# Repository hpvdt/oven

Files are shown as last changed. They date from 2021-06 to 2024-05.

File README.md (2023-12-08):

# Oven Control System

Our team's generic composite oven controller. Used to maintain a desired two-step curing 
cycle recommended for the majority of our composites. Each step is defined with a target 
temperature, a ramp speed to reach it at (e.g. 2 degC/minute), and hold time at that 
temperature.

The control system is pretty simple, a single K-type thermocouple is used to monitor the 
temperature in the oven, and a simple "ON/OFF" scheme is used to operate the relay that 
controls the power to the heater. Turning ON when below a threshold, and then OFF once 
the upper threshold is surpassed.

User input is handled by a 16 button keypad, with a 20 by 4 character LCD screen used for 
feedback to the user to inform them of their input, and the current state of the oven.

## Code

With the exception of the display code (under "libraries") all the code was written by hand 
in the Arduino IDE. The main firmware is `oven_system` which is written for an Arduino Nano.

It was previously modified to include logging capabilities (`oven_system_with_logging`), 
and another version to operate using the serial interface for input/output in the absence 
of a keybad and/or a screen (`oven_system_no_display`). ***These variants have not been 
maintained to include recent improvements to the main code!***

In addition to the main code, we also prepared unit tests for each piece of hardware we were 
introducing to the system. In these we wrote the code needed to interact with each part as 
well as running some basic tests to exercise both the code and component. These are all in 
the "unit_tests" folder.

## Hardware

The current design is a small circuit board which has the ATmega328P microcontroller and 
the MAX6675 thermocouple chip. The microcontroller is set up to be programmed just like 
an Arduino Nano. Off board is the solid state relay used to regulate the heater, the 5V 
supply, keypad, and screen. This is all housed in a metal case repurposed from a failed 
power supply, with the terminal block used to connect the thermocouple, power, and heater.

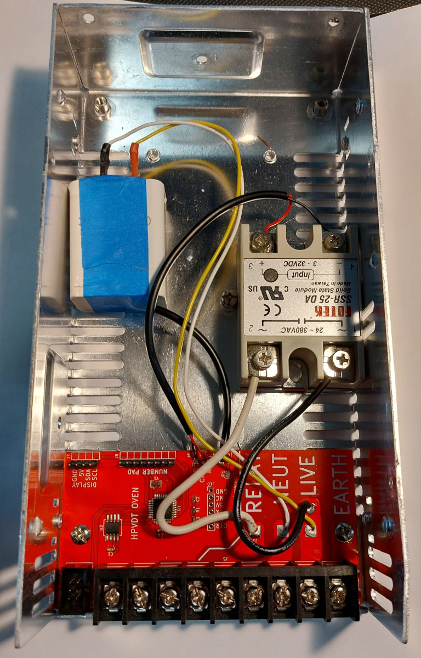
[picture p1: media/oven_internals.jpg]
The internal layout of the present oven system


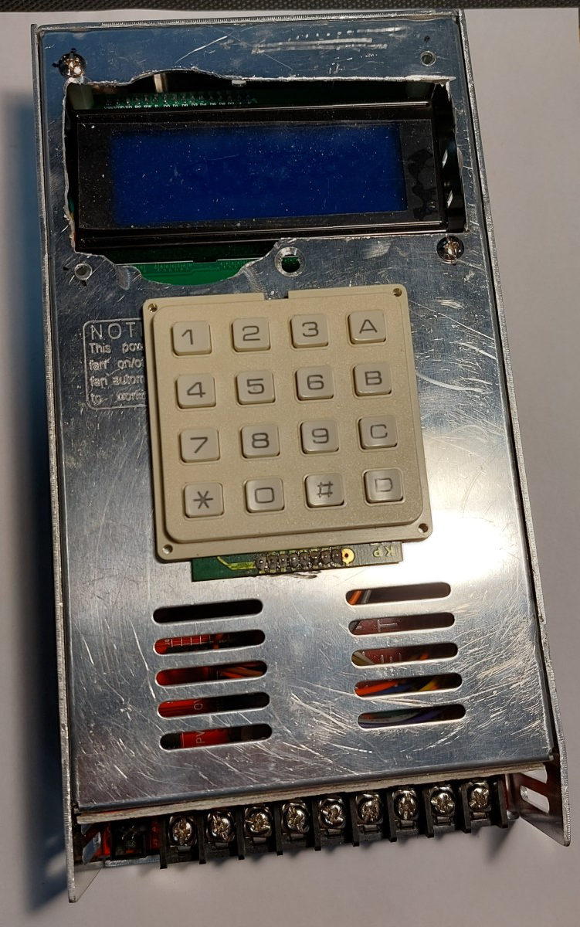
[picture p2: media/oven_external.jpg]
External view of the completed assembly


The current board was designed in KiCad 6, however my previous versions were designed in 
EAGLE. The most notable differences through iterations are:

- Embedding of the microcontroller and the MAX6675 directly to the main board
- Removal of the logging functionality since it was not used
- The earliest versions were designed to use thermistors instead of a thermocouple
- Previous designs weren't designed to fit in any particular enclosure

## TODO

A small to-do list of future features that could improve the system.

- [ ] Add some system to allow for recovery if power is interrupted
- [ ] Add some system to allow the system to be reset if needed
- [x] Figure out why SPI programming doesn't work if the MAX6675 is connected in any way
    - This was due to the MAX6675 not having a pullup on nCS, so it was active during programming of the ATmega and interfered on the SPI bus.
    - This **should** be revised in future hardware revisions

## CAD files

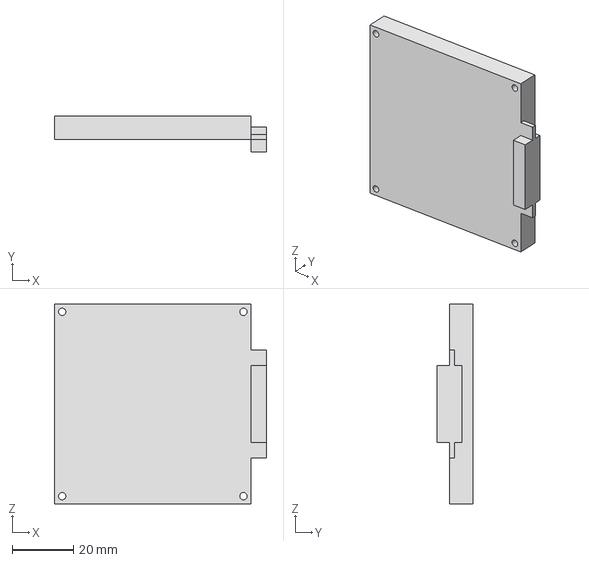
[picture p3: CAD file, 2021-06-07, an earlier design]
hardware/Old Hardware/CAD Files of Parts/Keypad.stp
69.0 x 11.6 x 65.0 mm

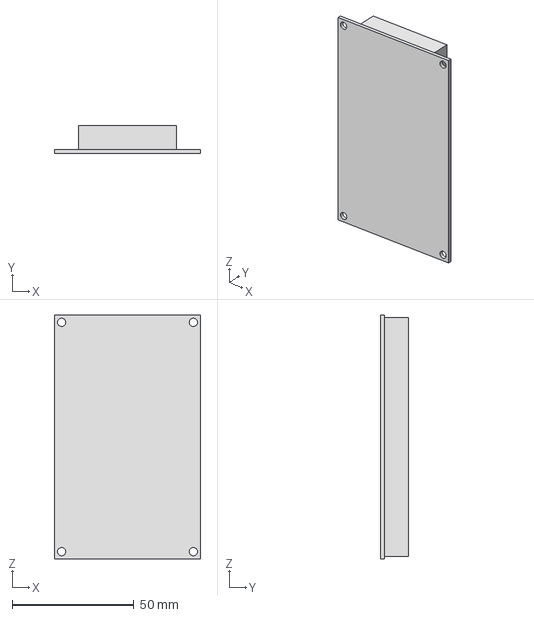
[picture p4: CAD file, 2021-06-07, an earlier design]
hardware/Old Hardware/CAD Files of Parts/LCD Screen.stp
60.0 x 11.6 x 100.0 mm

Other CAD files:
hardware/Old Hardware/CAD Files of Parts/Case.ipt
hardware/Old Hardware/CAD Files of Parts/Keypad.ipt
hardware/Old Hardware/CAD Files of Parts/LCD Screen.ipt
hardware/Old Hardware/CAD Files of Parts/OldVersions/Case.0002.ipt
hardware/Old Hardware/CAD Files of Parts/OldVersions/Keypad.0001.ipt
hardware/Old Hardware/CAD Files of Parts/OldVersions/LCD Screen.0001.ipt
hardware/Old Hardware/CAD Files of Parts/OldVersions/PCB.0001.ipt
hardware/Old Hardware/CAD Files of Parts/Oven Control.iam
hardware/Old Hardware/CAD Files of Parts/PCB.ipt

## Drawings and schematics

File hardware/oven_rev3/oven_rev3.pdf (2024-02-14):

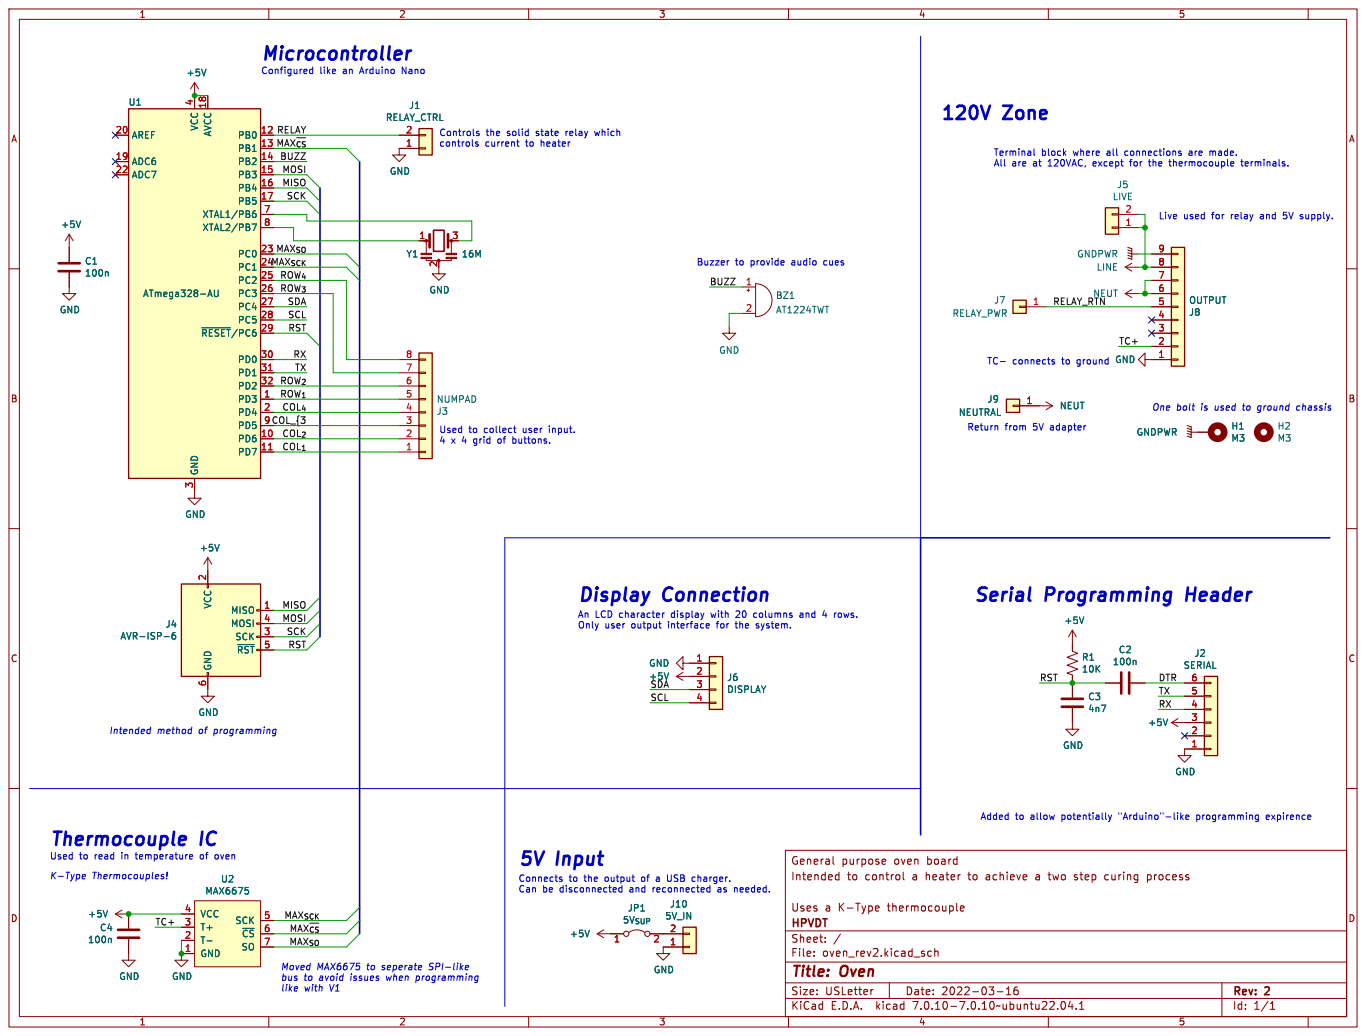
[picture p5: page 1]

BUZZ SCK
SCL MISO MOSI RST

Live used for relay and 5V supply.

2 SCK 3 MOSI 4 ~{RST}5 GND

Intended method of programming

Moved MAX6675 to seperate SPI-like
bus to avoid issues when programming
like with V1

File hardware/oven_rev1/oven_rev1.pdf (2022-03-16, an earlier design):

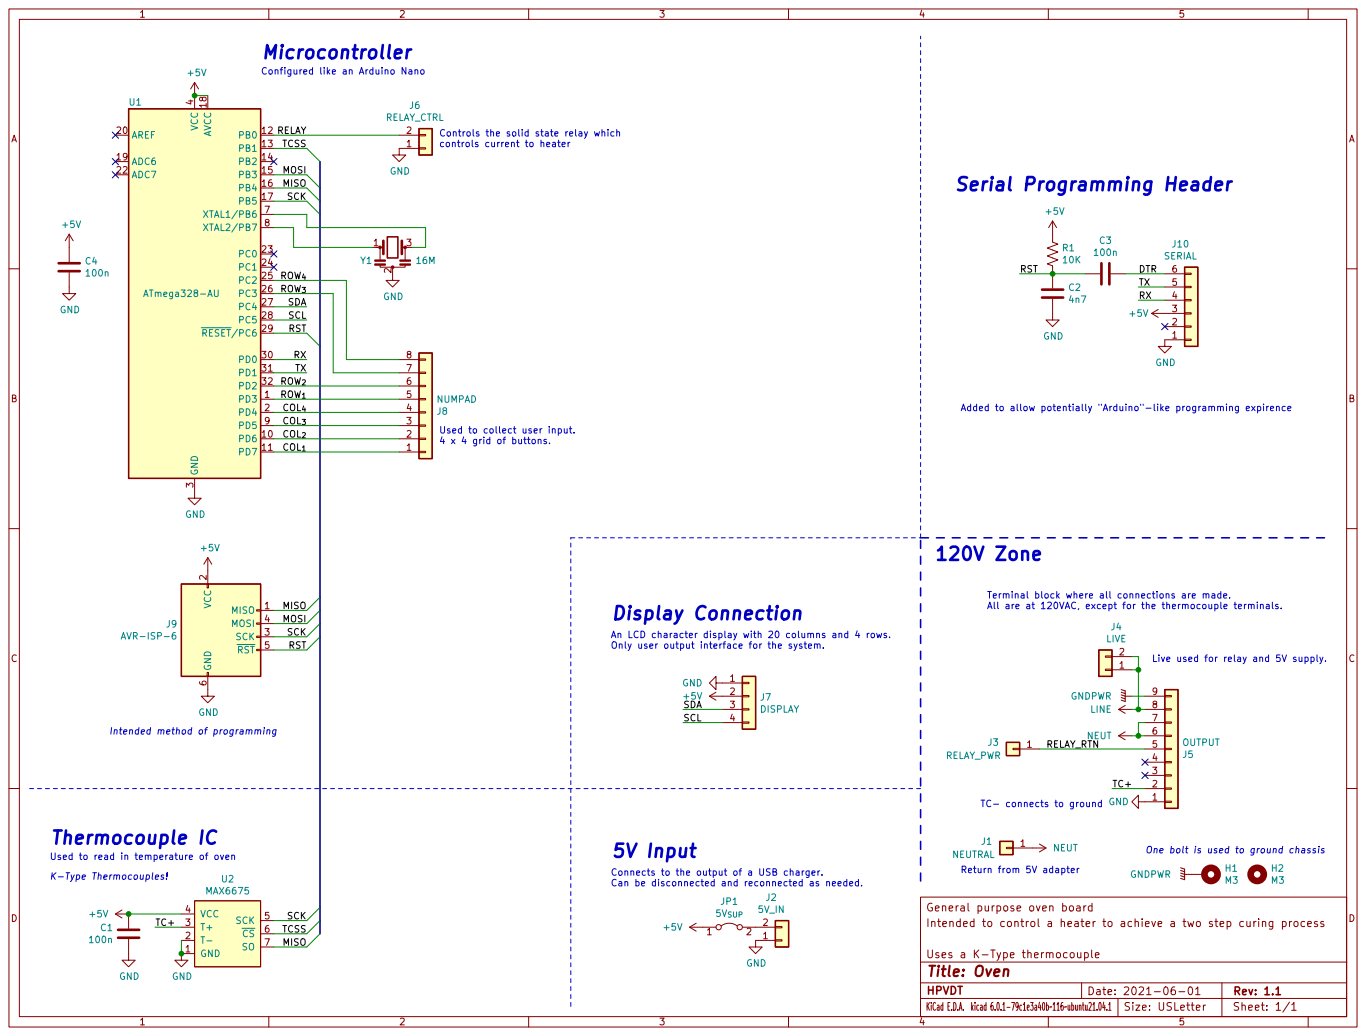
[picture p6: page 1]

Controls the solid state relay which controls current to heater Used to collect user input.

Configured like an Arduino Nano

3 PD0 30 PD1 31 PD2 32 VCC
ROW_{4} SDARX COL_{4} RST MISO MISO
SCK

Added to allow potentially "Arduino"-like programming expirence

COL_{3 | 3

COL_{1} | 1

2 SCK 3 MOSI 4 ~{RST} 5 GND

Live used for relay and 5V supply. Terminal block where all connections are made. All are at 120VAC, except for the thermocouple terminals.

An LCD character display with 20 columns and 4 rows.
Only user output interface for the system.

Intended method of programming

Connects to the output of a USB charger. Can be disconnected and reconnected as needed.

General purpose oven board KiCad E.D.A. kicad 6.0.1-79c1e3a40b~116~ubuntu21.04.1
Intended to control a heater to achieve a two step curing process

HPVDT Uses a K-Type thermocouple

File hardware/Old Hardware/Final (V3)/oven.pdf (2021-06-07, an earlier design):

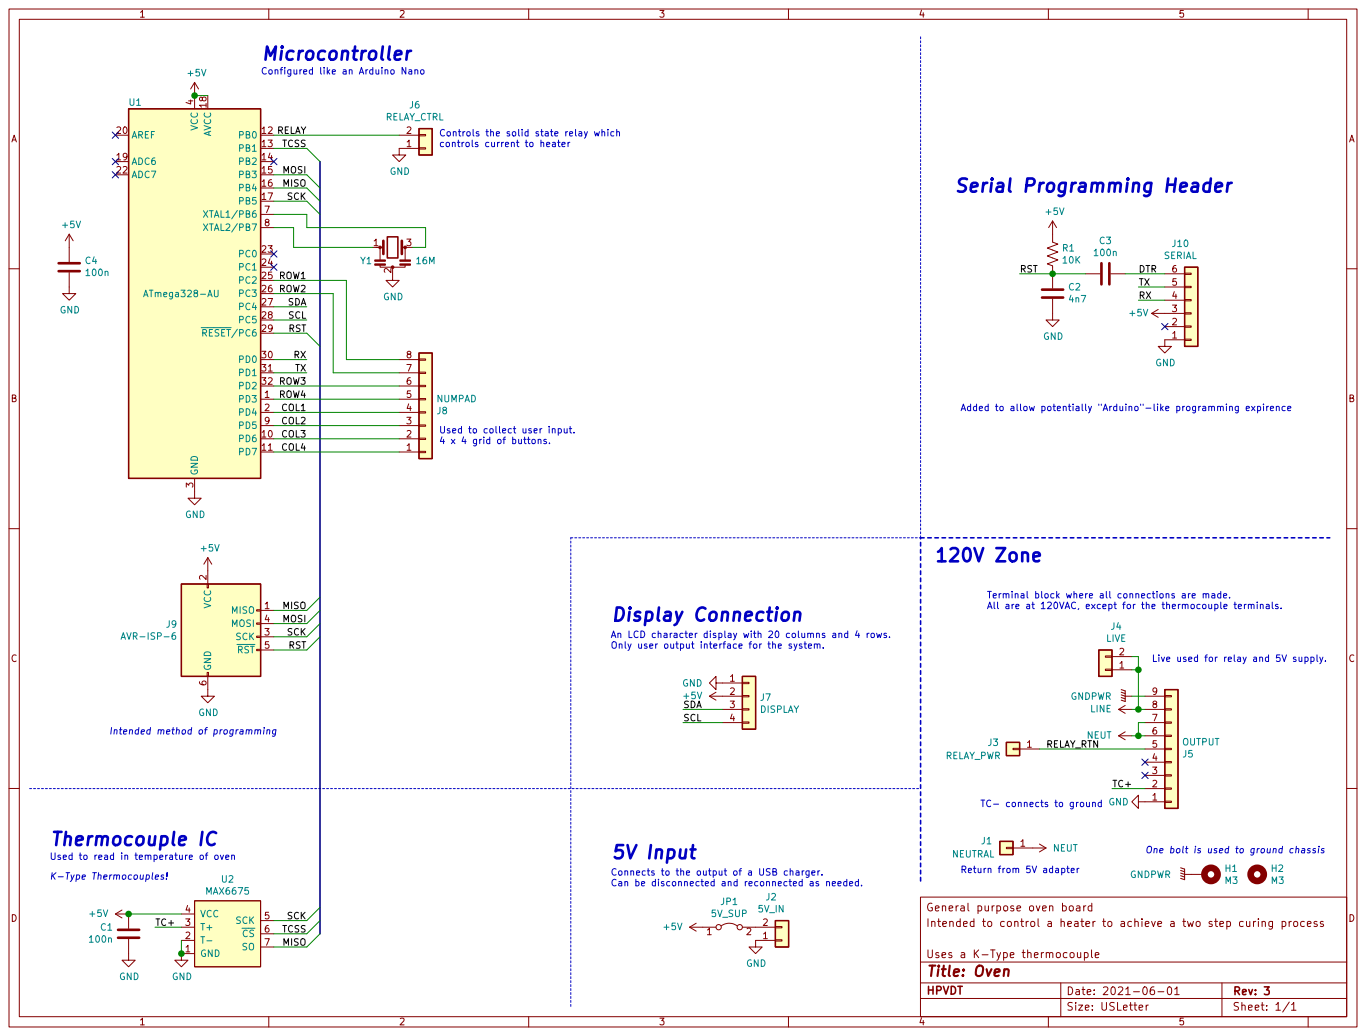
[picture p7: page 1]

Configured like an Arduino Nano

Added to allow potentially "Arduino"-like programming expirence

Used to collect user input.
4 x 4 grid of buttons.

2 SCK 3 MOSI 4 RST 5 GND

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

Intended method of programming

TC- connects to ground

One bolt is used to ground chassis

Connects to the output of a USB charger. Can be disconnected and reconnected as needed.

Intended to control a heater to achieve a two step curing process

HPVDT Uses a K-Type thermocouple

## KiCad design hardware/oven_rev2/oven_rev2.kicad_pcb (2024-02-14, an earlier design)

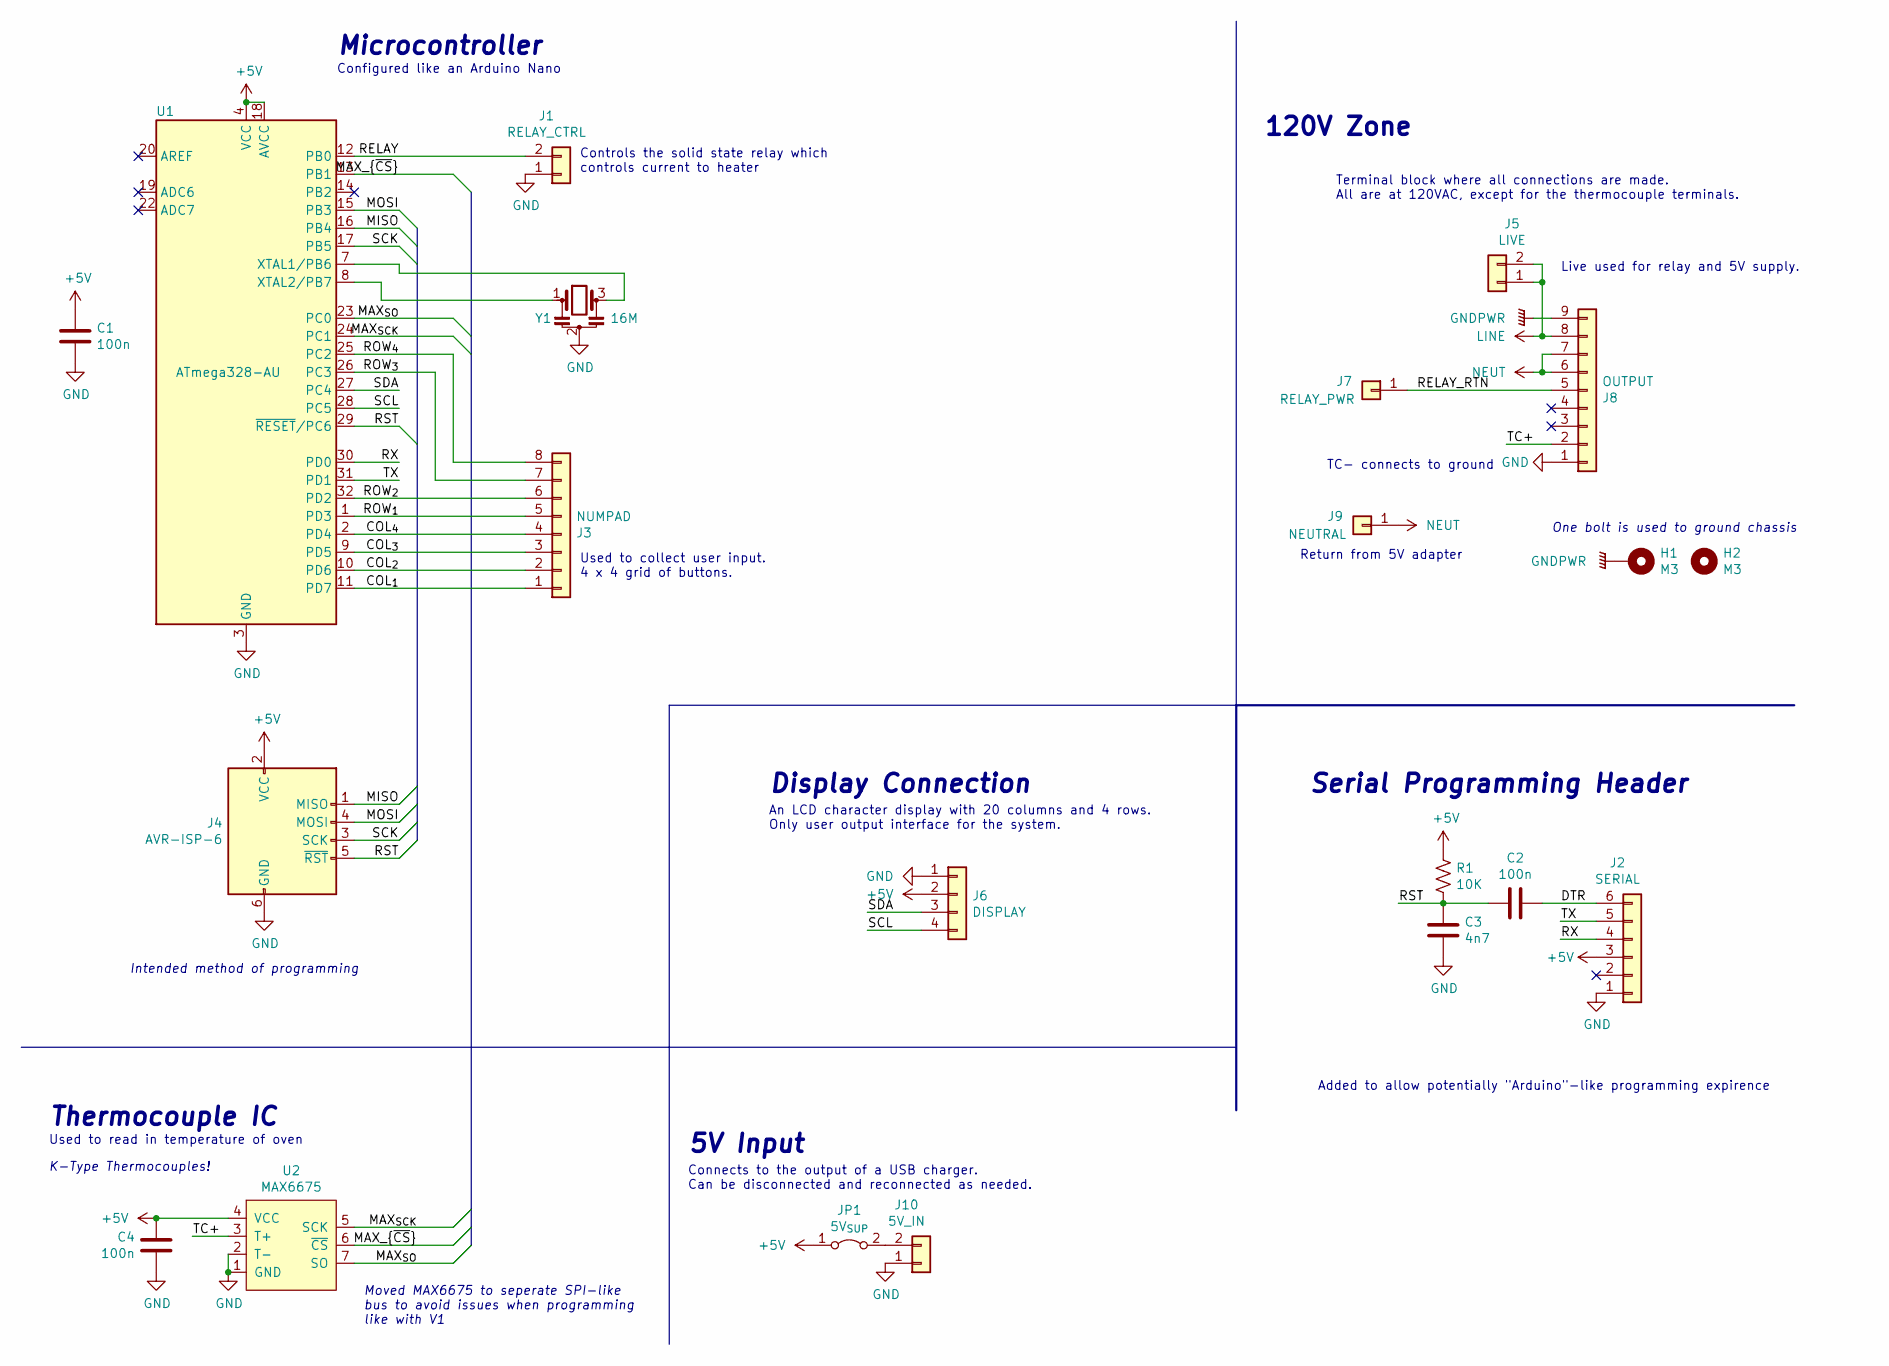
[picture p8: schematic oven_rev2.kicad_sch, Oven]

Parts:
C1, C2, C4: 100n; C_0603_1608Metric
C3: 4n7; C_0603_1608Metric
H1: M3; MountingHole_3.5mm_Pad_Via
H2: M3; MountingHole_3.5mm
J1: RELAY_CTRL; PinHeader_1x02_P2.54mm_Horizontal
J2: SERIAL; PinHeader_1x06_P2.54mm_Vertical
J3: NUMPAD; PinHeader_1x08_P2.54mm_Horizontal
J4: AVR-ISP-6; IDC-Header_2x03_P2.54mm_Vertical
J5: LIVE; SolderWire-2sqmm_1x02_P7.8mm_D2mm_OD3.9mm
J6: DISPLAY; PinHeader_1x04_P2.54mm_Horizontal
J7: RELAY_PWR; SolderWire-2sqmm_1x01_D2mm_OD3.9mm
J8: OUTPUT; 9POS-TERMBLOCK
J9: NEUTRAL; SolderWire-2sqmm_1x01_D2mm_OD3.9mm
J10: 5V_IN; PinHeader_1x02_P2.54mm_Horizontal
JP1: 5V_{SUP}; SolderJumper-2_P1.3mm_Bridged_Pad1.0x1.5mm
R1: 10K; R_0603_1608Metric
U1: ATmega328-AU; TQFP-32_7x7mm_P0.8mm
U2: MAX6675; SO-8_5.3x6.2mm_P1.27mm
Y1: 16M; Resonator_SMD_muRata_CSTxExxV-3Pin_3.0x1.1mm

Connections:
+5V: C1.2, C4.2, J2.3, J4.2 (VCC), J6.2, JP1.1 (A), R1.1, U1.4 (VCC), U1.6 (VCC), U1.18 (AVCC), U2.4 (VCC)
/COL_{1}: J3.1, U1.11 (PD7)
/COL_{2}: J3.2, U1.10 (PD6)
/COL_{3}: J3.3, U1.9 (PD5)
/COL_{4}: J3.4, U1.2 (PD4)
/DTR: C2.1, J2.6
/MAX_{SCK}: U1.24 (PC1), U2.5 (SCK)
/MAX_{SO}: U1.23 (PC0), U2.7 (SO)
/MAX_{~CS}: U1.13 (PB1), U2.6 (~CS)
/MISO: J4.1 (MISO), U1.16 (PB4)
/MOSI: J4.4 (MOSI), U1.15 (PB3)
/RELAY: J1.2, U1.12 (PB0)
/RELAY_RTN: J7.1, J8.5
/ROW_{1}: J3.5, U1.1 (PD3)
/ROW_{2}: J3.6, U1.32 (PD2)
/ROW_{3}: J3.7, U1.26 (PC3)
/ROW_{4}: J3.8, U1.25 (PC2)
/RST: C2.2, C3.2, J4.5 (~RST), R1.2, U1.29 (~RESET/PC6)
/RX: J2.4, U1.30 (PD0)
/SCK: J4.3 (SCK), U1.17 (PB5)
/SCL: J6.4, U1.28 (PC5)
/SDA: J6.3, U1.27 (PC4)
/TC+: J8.2, U2.3 (T+)
/TX: J2.5, U1.31 (PD1)
GND: C1.1, C3.1, C4.1, J1.1, J2.1, J4.6 (GND), J6.1, J8.1, J10.1, U1.3 (GND), U1.5 (GND), U1.21 (GND), U2.1 (GND), U2.2 (T-), Y1.2
GNDPWR: H1.1, J8.9
LINE: J5.1, J5.2, J8.8
NEUT: J8.6, J8.7, J9.1
unnamed: J10.2, JP1.2 (B)
unnamed: U1.7 (XTAL1/PB6), Y1.3
unnamed: U1.8 (XTAL2/PB7), Y1.1

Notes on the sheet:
Moved MAX6675 to seperate SPI-like bus to avoid issues when programming like with V1
One bolt is used to ground chassis
Live used for relay and 5V supply.
Used to read in temperature of oven
120V Zone
Controls the solid state relay which controls current to heater
Microcontroller
5V Input
Display Connection
Return from 5V adapter
Connects to the output of a USB charger. Can be disconnected and reconnected as needed.
Intended method of programming
An LCD character display with 20 columns and 4 rows. Only user output interface for the system.
Added to allow potentially "Arduino"-like programming expirence
TC- connects to ground
Configured like an Arduino Nano
Serial Programming Header
Thermocouple IC
K-Type Thermocouples!
Terminal block where all connections are made. All are at 120VAC, except for the thermocouple terminals.
Used to collect user input. 4 x 4 grid of buttons.

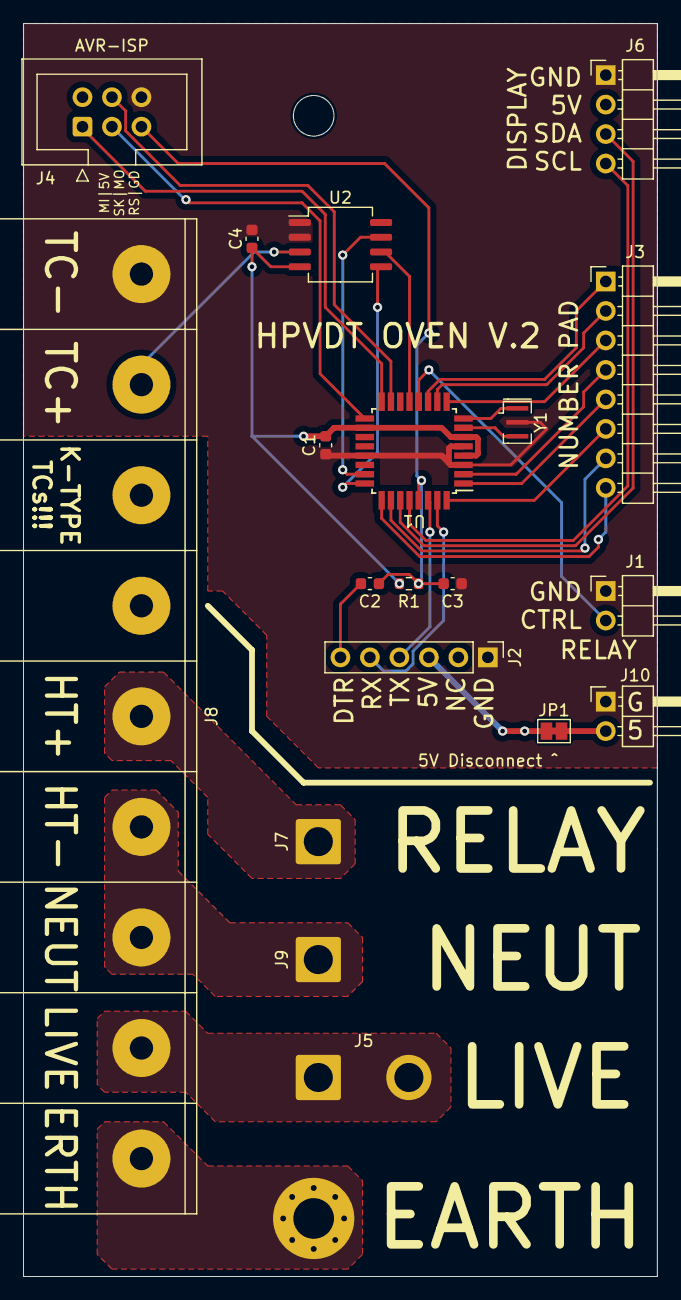
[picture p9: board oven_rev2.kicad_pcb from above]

Board: 2 copper layers, 54.6 x 108.0 mm, 21 parts (0 on the bottom side), 31 nets.

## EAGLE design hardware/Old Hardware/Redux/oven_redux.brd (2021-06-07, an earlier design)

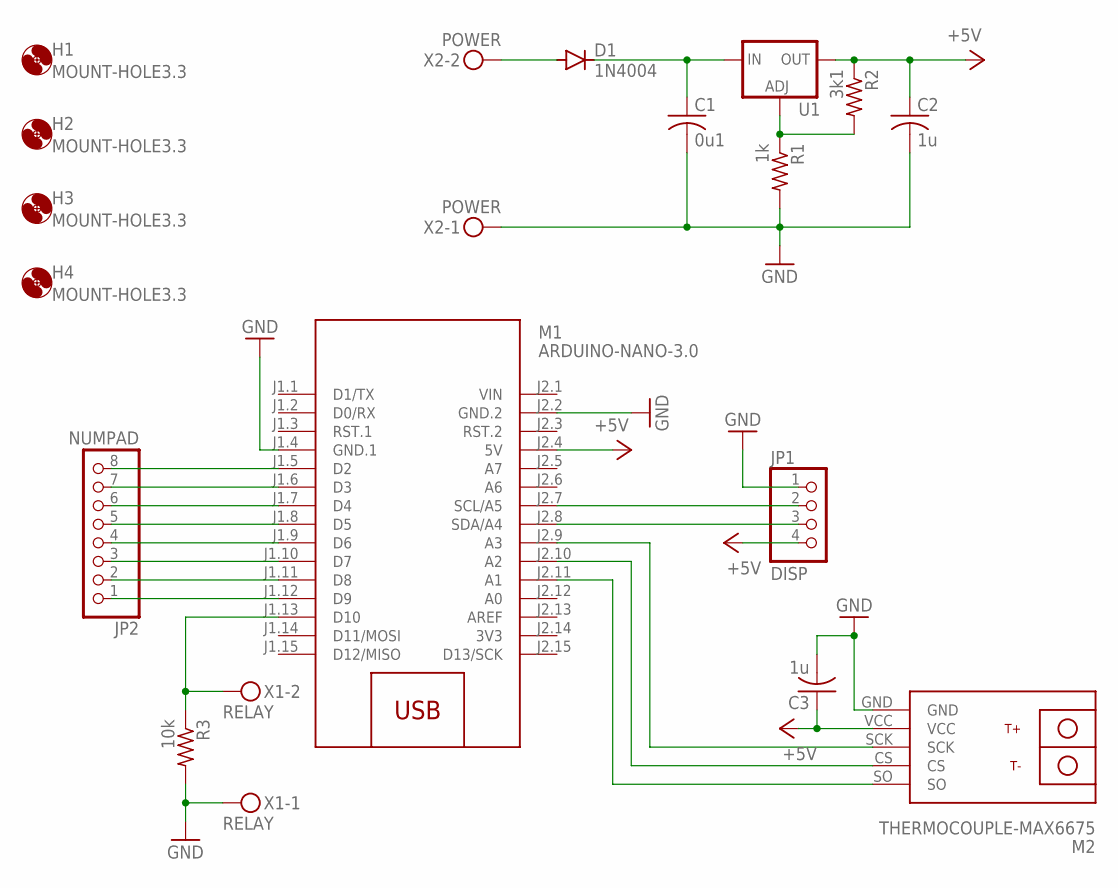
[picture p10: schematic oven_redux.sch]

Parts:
C1: 0u1; C025-050X050
C2, C3: 1u; C025-050X050
D1: 1N4004; DO41-10
H1, H2, H3, H4: MOUNT-HOLE3.3; 3,3
JP1: DISP; 1X04
JP2: NUMPAD; 1X08
M1: ARDUINO-NANO-3.0
M2: THERMOCOUPLE-MAX6675
R1: 1k; 0204/7
R2: 3k1; 0204/7
R3: 10k; 0204/7
U1: LM317TL; 317TL
X1: RELAY; MKDSN1,5/2-5,08
X2: POWER; MKDSN1,5/2-5,08

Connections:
3V3: M1.J2.14 (3V3)
+5V: C2.1, C3.1, JP1.4, M1.J2.4 (5V), M2.VCC, R2.1, U1.2 (OUT)
GND: C1.2, C2.2, C3.2, JP1.1, M1.J1.4 (GND.1), M1.J2.2 (GND.2), M2.GND, R1.2, R3.2, X1.1, X2.1
unnamed: JP2.1, M1.J1.12 (D9)
unnamed: JP2.2, M1.J1.11 (D8)
unnamed: JP2.3, M1.J1.10 (D7)
unnamed: JP2.4, M1.J1.9 (D6)
unnamed: JP2.5, M1.J1.8 (D5)
unnamed: JP2.6, M1.J1.7 (D4)
unnamed: JP2.7, M1.J1.6 (D3)
unnamed: JP2.8, M1.J1.5 (D2)
unnamed: JP1.2, M1.J2.7 (SCL/A5)
unnamed: R1.1, R2.2, U1.1 (ADJ)
unnamed: C1.1, D1.C, U1.3 (IN)
unnamed: D1.A, X2.2
unnamed: JP1.3, M1.J2.8 (SDA/A4)
unnamed: M1.J2.9 (A3), M2.SCK
unnamed: M1.J2.10 (A2), M2.CS
unnamed: M1.J1.13 (D10), R3.1, X1.2
unnamed: M1.J2.11 (A1), M2.SO
VIN: M1.J2.1 (VIN)

Board: 2 copper layers, 18 parts (0 on the bottom side), 19 nets, no tracks yet.

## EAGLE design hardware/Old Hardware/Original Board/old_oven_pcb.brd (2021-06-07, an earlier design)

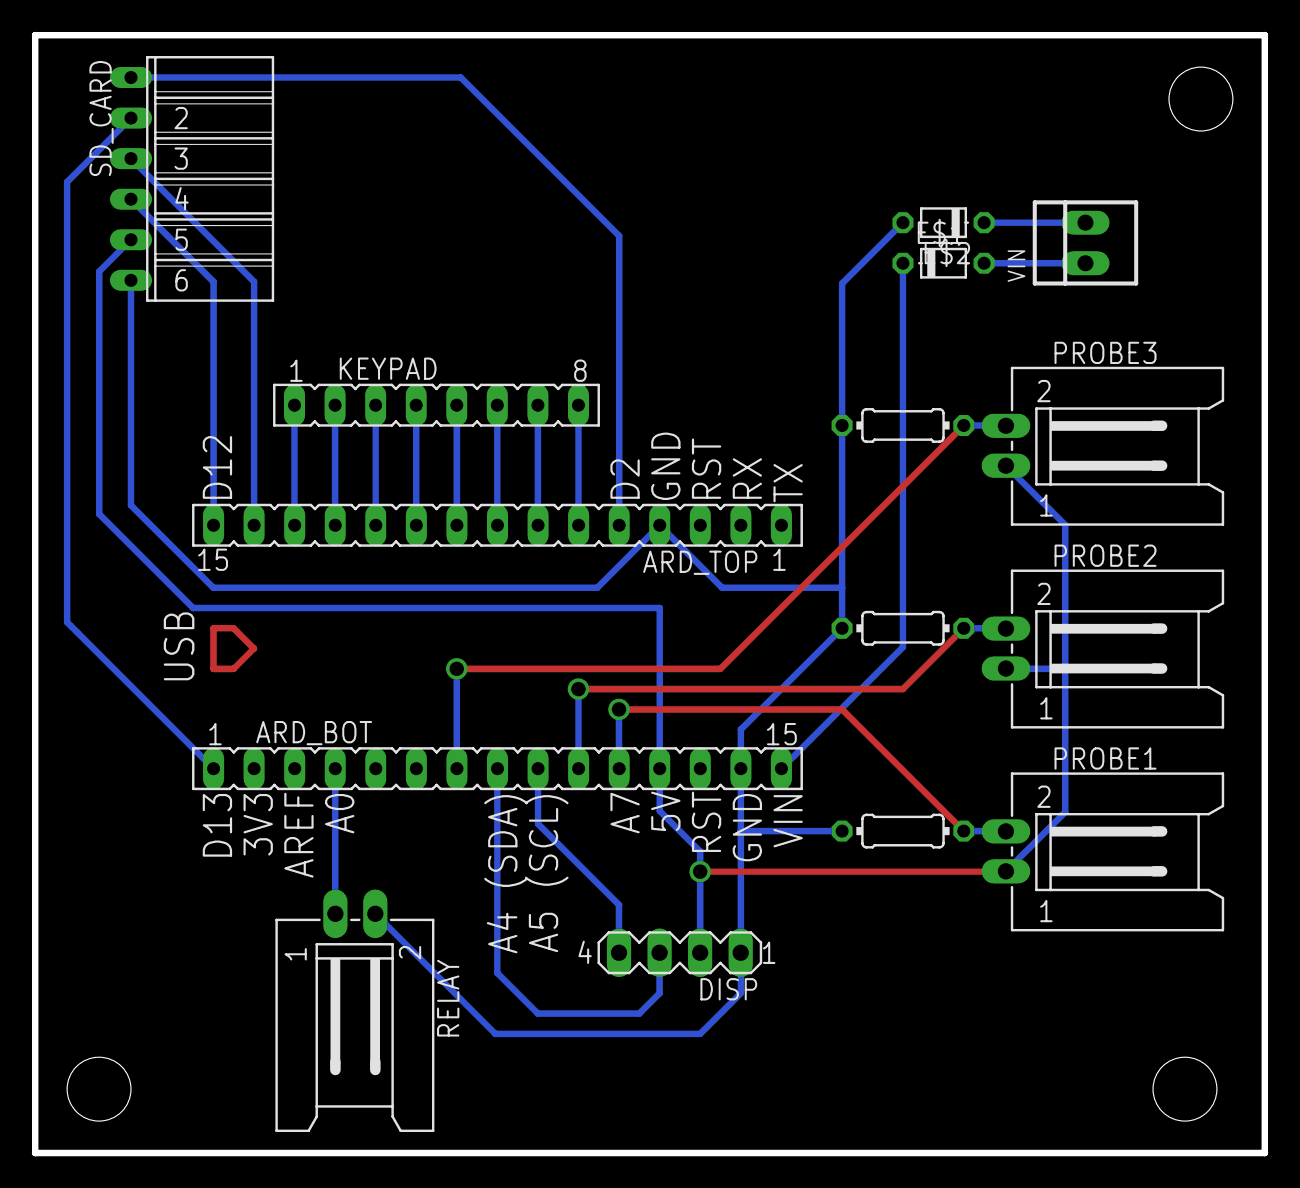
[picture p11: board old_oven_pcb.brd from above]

Board: 2 copper layers, 77.0 x 70.0 mm, 15 parts (0 on the bottom side), 23 nets.

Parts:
ARD_BOT: FE15
ARD_TOP: FE15
DISP: MA04-1
E$1, E$2: D-5
E$3, E$4, E$6: 10k; 0204/7
KEYPAD: FE08
PROBE1, PROBE2, PROBE3: L02P
RELAY: L02P
SD_CARD: FE06W
VIN: 22-23-2021

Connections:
5V: ARD_BOT.12, DISP.2, PROBE1.1, PROBE2.1, PROBE3.1, SD_CARD.5
D3: ARD_TOP.6, KEYPAD.8
D4: ARD_TOP.7, KEYPAD.7
D5: ARD_TOP.8, KEYPAD.6
D6: ARD_TOP.9, KEYPAD.5
D7: ARD_TOP.10, KEYPAD.4
D8: ARD_TOP.11, KEYPAD.3
D9: ARD_TOP.12, KEYPAD.2
D10: ARD_TOP.5, SD_CARD.1
D13: ARD_BOT.1, SD_CARD.2
GND: ARD_BOT.14, ARD_TOP.4, DISP.1, E$2.A, E$3.2, E$4.2, E$6.2, RELAY.2, SD_CARD.6
PROBE1: ARD_BOT.11, E$4.1, PROBE1.2
PROBE2: ARD_BOT.10, E$3.1, PROBE2.2
PROBE3: ARD_BOT.7, E$6.1, PROBE3.2
RELAY: ARD_BOT.4, RELAY.1
S$1: ARD_TOP.13, KEYPAD.1
S$3: ARD_TOP.15, SD_CARD.4
S$4: ARD_TOP.14, SD_CARD.3
SCL: ARD_BOT.9, DISP.4
SDA: ARD_BOT.8, DISP.3
V+: E$1.A, VIN.1
V-: E$2.C, VIN.2
VIN: ARD_BOT.15, E$1.C

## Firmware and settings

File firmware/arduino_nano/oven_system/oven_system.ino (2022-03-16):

#include <Wire.h>
#include <LiquidCrystal_I2C.h>

// A4 is SDA
// A5 is SCL

LiquidCrystal_I2C lcd(0x27, 2, 1, 0, 4, 5, 6, 7, 3, POSITIVE);
//LiquidCrystal_I2C lcd(0x27, 4, 5, 6, 0, 1, 2, 3, 7, POSITIVE);

// Keypad config
const byte row1 = 3; // Row 1 pin
const byte row2 = 2;
const byte row3 = A3;
const byte row4 = A2;
const byte col1 = 7; // Column 1 pin
const byte col2 = 6;
const byte col3 = 5;
const byte col4 = 4;

char buttonPressed;
// Keypad works by detecting the intersection of a row and col pulling down an input. (A column pulling the row down)

// MAX6675 Pins
const byte MAX_SCK = A1;
const byte MAX_CS = 9;
const byte MAX_SO = A0;

// Heater 
const byte heater = 12;  // Heater relay pin
bool heaterState;       // State variable

// Control variables
int screen, field;                  // Used for display
const int numScreens = 4;           // Used as a limit for number of distinct screens
const int numFields = 3;            // Used as a limit for number of fields on a screen

// User input field configuration
const int maxFieldLength = 6;        // Max length of entered data
String fields[9];                    // Used to display entry data (should have numFields * numScreens elements)

int stage = 1;                          // Records cooking stage
double targetTemp, curTemp;              // Target and current temp
double temperature[5];                   // Used to store temp set points
const double tempTol = 5;                // Used as tolerance for over temp - IMPORTANT
unsigned long setPointTimes[5];         // Used for changes
double elapsedTime;                      // Used for status display
String endTime;                         // Used for status display (to minimize repeated instructions)

void setup() {
  lcd.begin(20, 4);   // Set up display. 20 character in 4 rows
  lcd.clear();        //Clear the display

  // Keypad setup
  pinMode(row1, INPUT_PULLUP); pinMode(row2, INPUT_PULLUP); pinMode(row3, INPUT_PULLUP); pinMode(row4, INPUT_PULLUP);
  pinMode(col1, OUTPUT); pinMode(col2, OUTPUT); pinMode(col3, OUTPUT); pinMode(col4, OUTPUT);

  pinMode(heater, OUTPUT);            // Controls relay
  heaterState = LOW;                  // Off by default
  digitalWrite(heater, heaterState);

  // Splash screen
  printCenter(1, F("Oven Control System"));
  printCenter(2, F("Designed for HPDVT"));
  delay(1000);
  lcd.clear();

  // Initialization
  screen = 0;
  field = 0;
}

void loop() {
  // Screen
  switch (screen) {
    case 0: // Setup first point
      printLeft(0, F("Target Temp"));
      printLeft(1, F("Rise Rt. c/m"));
      printLeft(2, F("Hold Time (m)"));
      printCenter(3, F("Stg 1"));
      printCursor();
      for (int i = 0; i < numFields; i++) {
        printRight(i, fields[i + numFields * screen]);
      }
      printRight(3, "Stg 2>");

      buttonAction(); // Performs button action
      break;
    case 1: // Second point config
      printLeft(0, F("Target Temp"));
      printLeft(1, F("Rise Rt. c/m"));
      printLeft(2, F("Hold Time (m)"));
      printLeft(3, F("<Stg 1"));
      printCenter(3, F("Stg 2"));
      printCursor();
      for (int i = 0; i < numFields; i++) {
        printRight(i, fields[i + numFields * screen]);
      }
      printRight(3, "Strt>");

      buttonAction(); // Performs button action

      // Check if starting oven
      if (screen == (numScreens - 2)) {
        stage = 1; // Entered first stage
        
        //Sets temperature points
        temperature[0] = readTemperature(MAX_SCK, MAX_CS, MAX_SO); // Record starting temp
        temperature[1] = fields[0].toFloat();
        temperature[2] = temperature[1];
        temperature[3] = fields[numFields].toFloat();
        temperature[4] = temperature[3];

        // Gets times
        // Times are (target - start) / ramp rate
        elapsedTime = 0;
        setPointTimes[0] = actualMillis();                                                          // Start time
        setPointTimes[1] = (temperature[1] - temperature[0]) * 60000 / fields[1].toFloat();   // Uses rate and difference to find ramp time
        setPointTimes[2] = fields[2].toFloat() * 60000;                                       // Records hold time
        setPointTimes[3] = (temperature[3] - temperature[2]) * 60000 / fields[1].toFloat();   // Second ramp
        setPointTimes[4] = fields[2 + numFields].toFloat() * 60000;                           // Last hold

        for (int i = 1; i <= 4; i++) {
          setPointTimes[i] += setPointTimes[i - 1]; //Makes the times cummulative
        }
        endTime = int(ceil((setPointTimes[4] - setPointTimes[0]) / 60000)); // Records the end as a string for status display
      }
      break;
      
    case 2: // Runtime
      // Control
      // Gets linearly interpolated temperature based on time and bounding set points
      // map() outputs long int, needed floats so I adjusted their source code
      targetTemp = (actualMillis() - setPointTimes[stage - 1]) * (temperature[stage] - temperature[stage - 1]);
      targetTemp /= (setPointTimes[stage] - setPointTimes[stage - 1]);
      targetTemp += temperature[stage - 1];
      curTemp = readTemperature(MAX_SCK, MAX_CS, MAX_SO); // Gets current temp

      if (curTemp < targetTemp) {
        heaterState = HIGH;                   // Too cold
        digitalWrite(heater, heaterState);
      }
      else if (curTemp > (targetTemp + 1)) {
        heaterState = LOW;                    // Too hot
        digitalWrite(heater, heaterState);
      }
      
      // Time
      if (actualMillis() > setPointTimes[stage]) stage++; // Checks if approriate stage
      elapsedTime = actualMillis() - setPointTimes[0];    // Elaplsed time in ms
      elapsedTime /= 60000;                         // Elapsed time in minutes
      
      // Screen stuff
      printLeft(0, F("Cur/Tar"));
      printLeft(1, F("Elp/End"));
      printLeft(2, F("Heater"));
      printCenter(3, F("Oven Status"));

      // Fields
      fields[numFields * screen] = "  ";
      fields[numFields * screen] += oneDecimal(curTemp);       // Temp
      fields[numFields * screen] += "/";
      fields[numFields * screen] += oneDecimal(targetTemp);   // Target

      fields[1 + numFields * screen] = oneDecimal(elapsedTime);   // Time
      fields[1 + numFields * screen] += "/";
      fields[1 + numFields * screen] += endTime;                  // End

      if (heaterState) {
        fields[2 + numFields * screen] = " ON";  // Heater ON
      }
      else {
        fields[2 + numFields * screen] = "OFF"; // Heater OFF
      }

      for (int i = 0; i < numFields; i++) {
        printRight(i, fields[i + numFields * screen]);
      }

      // Check for finish (past stage 4)
      if (stage == 5) {
        screen++; // Go to next step
        lcd.clear();
        
        // Turn off heater
        heaterState = LOW;                  
        digitalWrite(heater, heaterState);
      }
      delay(300); // Extending cycle time during run time
      break;
      
    case 3: // Finished
      printCenter(0, F("Process Complete"));
      printCenter(1, F("Oven is disabled"));
      printLeft(3, "Cur. Temp");
      printRight(3, "   " + oneDecimal(readTemperature(MAX_SCK, MAX_CS, MAX_SO)));

      // Turn off heater
      heaterState = LOW;                  
      digitalWrite(heater, heaterState);
      
      delay(1000);
      break;
  }

  delay(25);
}

void buttonAction() {
  buttonPressed = checkKeypad(); // Get key pressed, if any
  
  switch (buttonPressed) {
    case 'x':
      break; // Nothing was pressed
      
    // Changing fields
    case 'A':
      field--;
      lcd.clear();
      field = constrain(field, 0, numFields - 1);
      break;
    case 'B':
      field++;
      lcd.clear();
      field = constrain(field, 0, numFields - 1);
      break;

    // Next screen
    case 'C':
      screen++;
      lcd.clear();
      screen = constrain(screen, 0, numScreens - 1);
      field = 0;
      break;
    case 'D':
      screen--;
      lcd.clear();
      screen = constrain(screen, 0, numScreens - 1);
      field = 0;
      break;

    // Backspace
    case '#':
      if (fields[field + numFields * screen].length() > 0) {
        lcd.clear();
        fields[field + numFields * screen].remove(fields[field + numFields * screen].length() - 1); // Removes last character
      }
      break;

    // Adding digits and decimal places is done by concatenating the string
    default:
      if (buttonPressed == '*') {
        buttonPressed = '.'; // Decimal
      }
      // Only adds if not at full length
      if ( fields[field + numFields * screen].length() < maxFieldLength){
        fields[field + numFields * screen] += buttonPressed;
      }
      break;
  }
}

// Function used to return a better approximation of time elasped
unsigned long actualMillis() {
  unsigned long trueMillis = millis();

  // millis() returns roughly 971 "milliseconds" per actual second due to the way millis() is set up with timers.
  // Scaling it up by a factor of 1.024 is needed to get roughly 1000 counts per actual second.
  // To keep it to integer math dividing by 125, multiplying by 128 is used.
  
  trueMillis = trueMillis / 125;
  trueMillis = trueMillis * 128;
  
  // Multiplication after division to avoid overflows with long work times
  
  return trueMillis;
}

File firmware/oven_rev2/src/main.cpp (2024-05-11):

#include <Arduino.h>
#include <Wire.h>
#include <LiquidCrystal_I2C.h>

#include "display.hpp"
#include "keypad.hpp"
#include "main.hpp"
#include "temperature.hpp"
#include "watchdog.hpp"

// Heater 
const byte heater = PIN_PB0;          // Heater relay pin
bool heaterState;                     // Heater state

// Control variables
int screen, field;                    // Used for display state
const int numScreens = 4;             // Used as a limit for number of distinct screens
const int numFields = 3;              // Used as a limit for number of fields on a screen

// User input field configuration
const int maxFieldLength = 6;         // Max length of entered data
String fields[numFields][numScreens]; // Data fields on each screen

int bakeStage = 1;                    // Records baking stage
float temperature[5];                 // Stores temperature set points
const float tempTol = 3.0;            // Tolerance for under temperature - IMPORTANT!
unsigned long setPointTimes[5];       // Records time for changes
String endTime;                       // Used for status display (to minimize repeated calculation)

void setup() {
  disableWatchdog(); // Needs to go first to prevent repeated watchdog resets

  setupKeypad();
  setupTemperature();

  // Set heater to start off until programmed
  pinMode(heater, OUTPUT);
  heaterState = LOW;
  digitalWrite(heater, heaterState);

  setupDisplay();

  screen = 0;
  field = 0;

  enableWatchdog(); 
  // NOTE: Currently the screen will shutdown until a complete power cycle after WDT reset
}

void loop() {
  // Screen
  switch (screen) {
    case 0: // Setup first point
      printLeft(0, F("Target Temp"));
      printLeft(3, oneDecimal(readTemperature()) + "C "); // Show temp on initial screen for error check
      printLeft(1, F("Rise Rt. c/m"));
      printLeft(2, F("Hold Time (m)"));
      printCenter(3, F("Stg 1"));
      printCursor();
      for (int i = 0; i < numFields; i++) printRight(i, fields[i][screen]);
      printRight(3, "Stg 2>");

      heaterState = LOW;

      buttonAction(); // Performs button action
      break;
    case 1: // Second point config
      printLeft(0, F("Target Temp"));
      printLeft(1, F("Rise Rt. c/m"));
      printLeft(2, F("Hold Time (m)"));
      printLeft(3, F("<Stg 1"));
      printCenter(3, F("Stg 2"));
      printCursor();
      for (int i = 0; i < numFields; i++) printRight(i, fields[i][screen]);
      printRight(3, "Strt>");

      heaterState = LOW;

      buttonAction(); // Performs button action

      // Check if starting oven
      if (screen == (numScreens - 2)) {
        bakeStage = 1; // Entered first stage
        
        //Sets temperature points
        temperature[0] = readTemperature(); // Record starting temp
        temperature[1] = fields[0][0].toFloat();
        temperature[2] = temperature[1];
        temperature[3] = fields[0][1].toFloat();
        temperature[4] = temperature[3];

        // Gets times
        // Times are (target - start) / ramp rate
        setPointTimes[0] = actualMillis();                                                      // Start time
        setPointTimes[1] = (temperature[1] - temperature[0]) * 60000 / fields[1][0].toFloat();  // Uses rate and difference to find ramp time
        setPointTimes[2] = fields[2][0].toFloat() * 60000;                                      // Records hold time
        setPointTimes[3] = (temperature[3] - temperature[2]) * 60000 / fields[1][1].toFloat();  // Second ramp
        setPointTimes[4] = fields[2][1].toFloat() * 60000;                                      // Last hold

        // If there is no second stage (signified by having the second stage temp < first)
        if (temperature[3] < temperature[1]) {
          temperature[3] = temperature[2];
          temperature[4] = temperature[2];
          setPointTimes[3] = 0;
          setPointTimes[4] = 0;
        }

        for (int i = 1; i <= 4; i++) setPointTimes[i] += setPointTimes[i - 1]; // Makes the times cummulative
        endTime = int(ceil((setPointTimes[4] - setPointTimes[0]) / 60000)); // Records the end as a string for status display
      }
      break;
      
    case 2: // Runtime
      // Control
      // Gets linearly interpolated temperature based on time and bounding set points
      // map() outputs long int, needed floats so I adjusted their source code
      float targetTemp, curTemp;
      curTemp = readTemperature();
      targetTemp = (actualMillis() - setPointTimes[bakeStage - 1]) * (temperature[bakeStage] - temperature[bakeStage - 1]);
      targetTemp /= (setPointTimes[bakeStage] - setPointTimes[bakeStage - 1]);
      targetTemp += temperature[bakeStage - 1];

      if (curTemp < (targetTemp - tempTol)) heaterState = HIGH;
      else if (curTemp > targetTemp) heaterState = LOW;
      
      // Time
      float elapsedTime;
      elapsedTime = actualMillis() - setPointTimes[0];            // Elaplsed time in ms
      if (elapsedTime > setPointTimes[bakeStage]) bakeStage++;    // Checks if approriate stage
      elapsedTime /= 60000;                                       // Elapsed time in minutes
      
      // Screen stuff
      printLeft(1, F("Cur/Tar"));
      printLeft(2, F("Elp/End"));
      printLeft(3, F("Heater"));
      printCenter(0, F("Oven Status"));

      // Fields
      fields[0][screen] = "  ";
      fields[0][screen] += oneDecimal(curTemp);
      fields[0][screen] += "/";
      fields[0][screen] += oneDecimal(targetTemp);

      fields[1][screen] = oneDecimal(elapsedTime);
      fields[1][screen] += "/";
      fields[1][screen] += endTime;

      if (heaterState) fields[2][screen] = " ON";
      else fields[2][screen] = "OFF";

      for (int i = 0; i < numFields; i++) printRight(i + 1, fields[i][screen]);

      // Check and handle reset condition
      if (checkKeypad() == 'E') {
        setupDisplay();
        screen = 0;
        field = 0;
        heaterState = LOW;
      }

      // Check for finish (past stage 4)
      if (bakeStage > 4) {
        screen++;
        lcd.clear();
      }
      delay(300); // Extending cycle time during run time
      break;
      
    case 3: // Finished
      printCenter(0, F("Process Complete"));
      printCenter(1, F("Oven is disabled"));
      printLeft(3, "Cur. Temp");
      printRight(3, "   " + oneDecimal(readTemperature()));

      heaterState = LOW; // Turn off heater for safety
      
      delay(200); // Slow down code in cooldown period
      break;
  }

  digitalWrite(heater, heaterState);
  delay(25);

  resetWatchdog();
}
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

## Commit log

2021-06-07 Upload of hardware files
    [Case.0002.ipt, Case.ipt, Keypad.0001.ipt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]
2021-06-15 Accounting for millis() inaccuracy
2022-03-16 Reworking hardware folder
    [Case.0002.ipt, Case.ipt, Keypad.0001.ipt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]
2022-03-16 Uploaded reorganized hardware folder
    [Case.0002.ipt, Case.ipt, Keypad.0001.ipt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]
2022-03-16 Accomodate new board design in code
2022-03-25 Updated oven revision to have buzzer
    [oven_v2.kicad_pcb, oven_v2.kicad_sch]
2024-02-14 Changed hardware organisation, updated to KiCad 7
    [oven_rev1-B_Cu.gbl, oven_rev1-B_Mask.gbs, oven_rev1-B_Paste.gbp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]
2024-02-14 Started rev 3 project
    [oven_rev3-B_Cu.gbl, oven_rev3-B_Mask.gbs, oven_rev3-B_Paste.gbp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]
2024-02-14 Removed unrelated gerbers from rev 3
    [oven_rev3-B_Cu.gbl, oven_rev3-B_Mask.gbs, oven_rev3-B_Paste.gbp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]
2024-02-14 Moved Arduino code into a directory
2024-02-14 Added KiCad `.gitignore`
2024-02-14 Generalized the temperature code
2024-02-14 Added support for switching between MAX chips
2024-02-14 Fixed logic for second ramp
    [main.cpp]
2024-02-14 Tidied up main code
    Lots of small changes:
    - Made lots of one line control statements single line
    - Changed `fields` to be a two dimensional array for easier reading
    - Changed code to avoid over shooting rather than undershooting (with configurable tolerance)
    [main.cpp]
2024-02-14 Touched up title blocks and rev 3
    [oven_rev1.kicad_sch, oven_rev3.kicad_sch]
2024-02-14 Minor touchups for titleblocks
    [oven_rev1.kicad_pcb, oven_rev1.kicad_sch, oven_rev3.kicad_pcb]
2024-02-14 Removed buzzer that was not present in fabricated boards
    [oven_rev2.kicad_pcb, oven_rev2.kicad_sch]
2024-02-14 Fixed pin allocations for rev 2 board
    [main.cpp]
2024-02-14 Minor touchups for temperature reading
2024-05-11 Extended watchdog timer to allow reset to be keyed
2024-05-11 Can skip second stage
    Added ability to skip second stage is only a single stage cure is desired by having the second stage temperature lower than the first
    [main.cpp]

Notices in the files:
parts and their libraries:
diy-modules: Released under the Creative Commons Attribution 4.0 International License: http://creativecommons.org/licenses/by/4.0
